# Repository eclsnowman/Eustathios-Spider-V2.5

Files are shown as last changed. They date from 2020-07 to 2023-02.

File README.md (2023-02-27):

# Eustathios-Spider-V2.5
V2.5 of Eustathios Spider (Includes Many Community Mods)

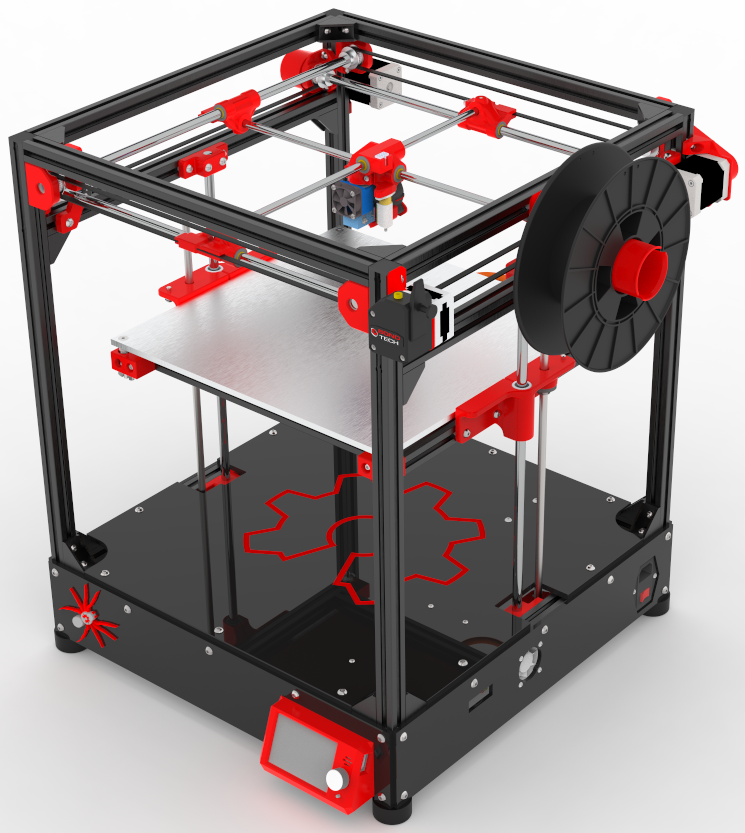
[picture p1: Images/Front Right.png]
Eustathios Spider - V2.5 Render Image


Hello and welcome to my Github for Eustathios Spider V2.5 3D printer. This printer is an updated version of the original Eustathios Spider, Eustathios Spider 2.0, and the addition of Community Modifications which have improved the design. The community added so many great improvements to this design, and I wanted to share an updated design that integrates all these wonderful improvements to the design, form, and function of this printer. I also wanted to update the design with newer more modern controls and components which have become available since the initial design.

This design stands on the shoulders of many great designers of Crossrod Gantry Printers that came before it. Most notable of these is the design of the original Eustathios by Jason Smith. This family of printers had a very devoted community in the G+ heydays, but now that Google+ has died the Community around the HercuLien printer and the Eustathios printer have moved to: https://forum.makerforums.info/c/herculien . This is thanks in great part to Michael K Johnson, who worked his magic to retain the years of great community interaction on G+ and ported it into the Discourse community over on Makerforums. If you are looking for support or community interaction on these printers moving forward, this is the place to go.

This family of printers is all based on the X/Y gantry mechanics of the Ultimaker. Ultimaker style mechanics utilizes a light hot-end/carriage which gets constrained by one X and one Y cross rod. Connected to these crossrods are rod ends which ride on side shafts that act both for power transmission of one axis (rotation) and as the linear guide for travel of the other axis (translation).

 Originally a gentleman who goes by the name Sublime (https://github.com/Intrinsically-Sublime/Tantillus/) created a small format variant of the Ultimaker mechanics which he called the Tantillus. Then GoopyPlastic (aka Brad Hill) created an extrusion version of the Tantillus called the Tslot Tantillus (https://github.com/goopyplastic/tslot-tantillus). Following in Brad’s footsteps Tim Rastall (https://plus.google.com/u/0/+TimRastall/posts) created the very popular Ingentis printer (https://www.youmagine.com/designs/ingentis-a-tantillus-variant) which is a larger version of Tantilus using thicker linear guide components, spectra drive system, and a much larger build envelope. The next printer in this design family was by Jason Smith (https://plus.google.com/u/0/103009815307828556107/posts) call the Eustathios (https://github.com/jasonsmit4/Eustathios). This is the printer that got me excited about this family of printers. Jason made several design choices like GT2 belts which I felt were great upgrades to the platform. I lucked out because his release was timed perfectly with a promotion Misumi was running where your first order from them up to $150 in value was free. I wanted to be able to modify Jason’s files slightly, but he had modeled everything in Sketchup. My limited experience was with Solidworks (self taught) so rather than learn new software I redrew Jason’s Eustathios design files from scratch. And so my Eustathios Spider V1 variant , named due to the color scheme, was born (https://github.com/eclsnowman/Lien3D_Eustathios_Spider). I built the Eustathios and fell in love with the smooth operation, clean prints, and overall reliability. So after operating the Eustathios for several months I converted my existing large CoreXY Printer (https://github.com/eclsnowman/Lien3D_CoreXY ) into a X/Y gantry printer with larger cross rods and dual extrusion. The name of this printer is HercuLien (https://github.com/eclsnowman/HercuLien). Prior to this latest revision (V2.5) there was the Eustathios Spider V2 which can be found here: https://github.com/eclsnowman/Eustathios-Spider-V2

I apologize for the long history lesson, but as you can see there is a lot of progress and talented people involved in these projects. I want to make sure credit is properly attributed to the many great makers who have come before me. The caliber of people involved and all the creativity in the platform is what keeps me so motivated. I would like to specifically mention some of the wonderful community members who added to this project over the years which have inspired or directly contributed to the Eustathios project. 

Specifically:

1.) Walter Hsiao (https://www.thingiverse.com/walter/about) for his elegant designs on the bed leveling corners, passthrough corner 6900-2RS bearing blocks, and Z Axis Bed Supports which have been integrated into the current design. In addition to these parts Walter has many additional designs for alternative components which can be used on the Eustathios like his Space Invaders Center Carriage, his Flying Extruder, and tons more. He is a prolific designer and his ability to simplify a design to its core and make it look elegant in the process inspires me and pushes me in my own designs. 

2.) Next, I would like to thank Zane Baird (https://www.linkedin.com/in/zane-baird-59096923). Over the years on Google Plus, at MRRF, and via Hangouts I am lucky to call Zane a friend. He made numerous design improvements which he implemented on his HercuLien printer. Like Water, Zane has a design style and elegance which is beyond my own ability. His designs for the Center Carriage and Side Carriages strike an balance between style and function which makes this V2.5 of the printer better than ever. Not only do these components work better and improve servicability, but they increase the printable area from previous design. Zanes input and passion on the project pushed me to do better in my own designs. I thank him for his friendship, inspiration and knowledge.

There are of course many more people to thank through this process: Martin Bondéus of Bondtech (who is a true friend with a brilliant mind), Roy Cortes from Panucatt (his boards and components are second to none), everyone from the G+ and Makerforums.info communities (Joe Spanier and Ray Kholodovsky I am looking at you), SeeMeCNC and John Olafson for years of inspiration and community through MRRF, and countless others. I can't name everyone, but you know who you are. Thank you, without you my journey of 3D Printing would not have been so fulfilling and so enjoyable.

Eustathios Spider V2.5 Overview:

* Max Travel Limits (X = 312mm / Y = 314mm / Z = 306mm)
* Designed Print Area (300mm x 300mm x 300mm)
* 32bit Controller = SKR V1.4 running Marlin 2
* TMC2209 Drivers (Qty:5) Independant Z for Marlin Auto Tram
* 24V Power with 500W Mains Powered Bed controled via SSR Relay
* Endstops:
   X&Y = switches or TMC Endstopless homing
   Z = single or dual switches, or BLTouch/3DTouch homing
* Leveling:
   Manual with endstops or autolevel w/ BLTouch/3DTouch

Documentation:

BOM = https://github.com/eclsnowman/Eustathios-Spider-V2.5/raw/master/BOM/ES25%20BOM.xlsx

Printable STL Parts = https://github.com/eclsnowman/Eustathios-Spider-V2.5/tree/master/3D%20Models/STL

Solidworks Files = https://github.com/eclsnowman/Eustathios-Spider-V2.5/tree/master/3D%20Models/Solidworks

Other 3D model formats in zip due to github file size limit) = https://github.com/eclsnowman/Eustathios-Spider-V2.5/tree/master/3D%20Models

Onshape Link: https://cad.onshape.com/documents/dcaaf87ad04323c8f9846c66/w/0537fe6b9eb1e2bc47668a76/e/4ce5ea03b6ef98527d9025d3

3D renders: https://github.com/eclsnowman/Eustathios-Spider-V2.5/tree/master/Images

Image of printed parts:

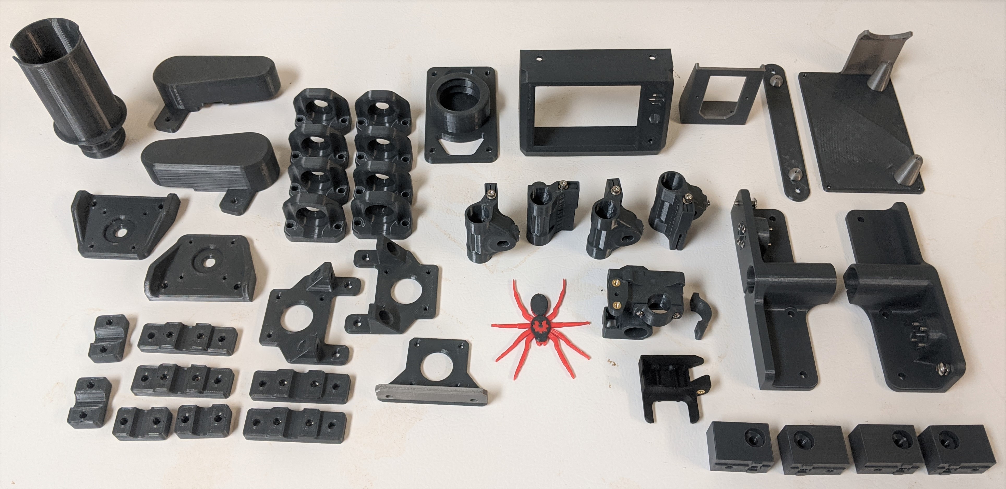
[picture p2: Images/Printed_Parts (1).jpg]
Eustathios Spider - V2.5 Printed Parts Image


Additional Renders:

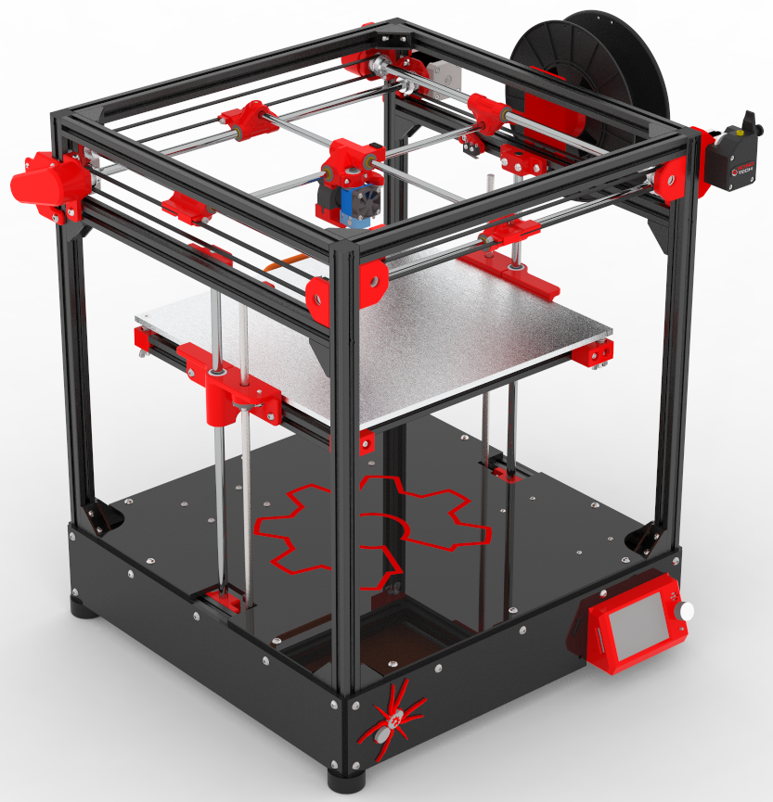
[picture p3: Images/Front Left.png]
Eustathios Spider - V2.5 Render2


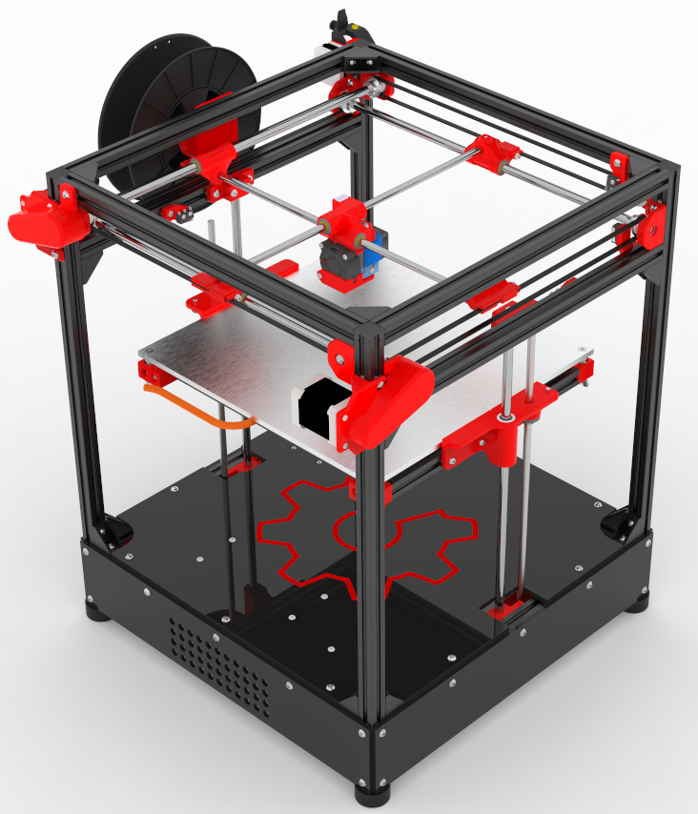
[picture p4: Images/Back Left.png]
Eustathios Spider - V2.5 Render3


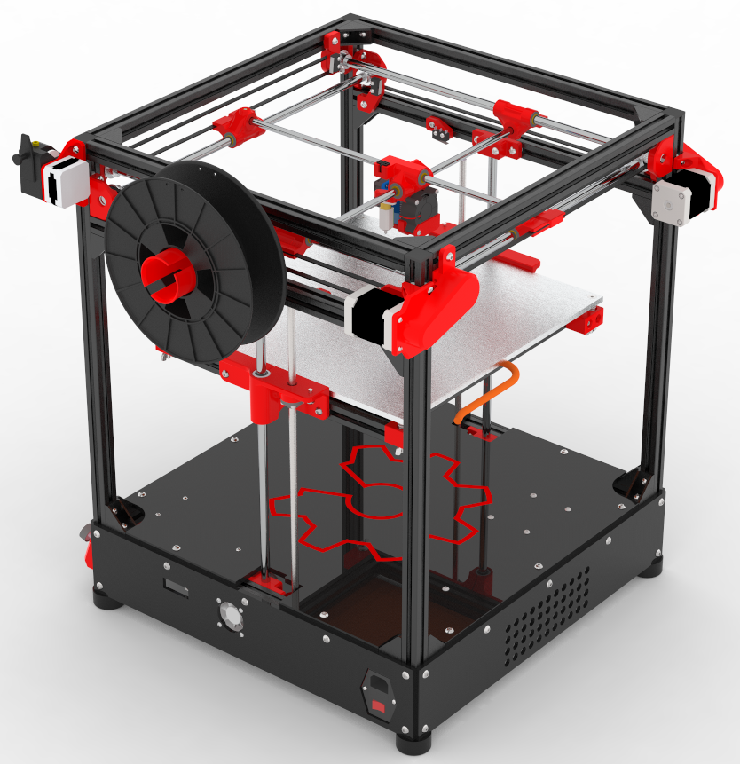
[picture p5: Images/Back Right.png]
Eustathios Spider - V2.5 Render4


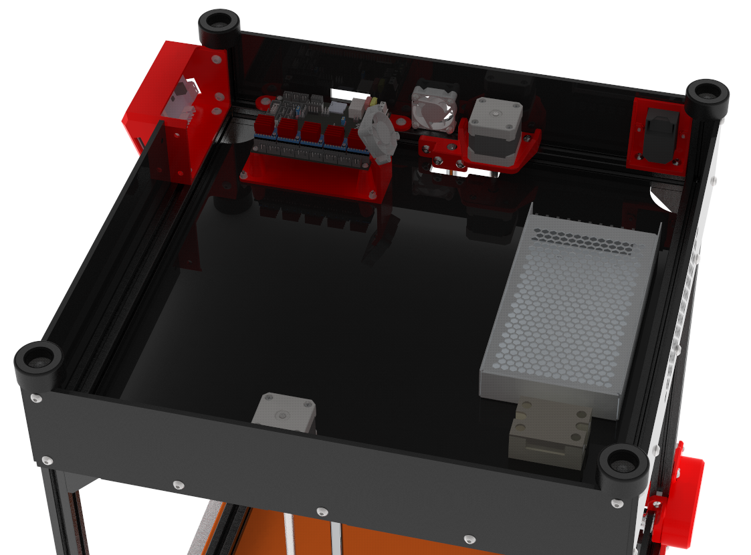
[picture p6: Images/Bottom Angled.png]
Eustathios Spider - V2.5 Render5


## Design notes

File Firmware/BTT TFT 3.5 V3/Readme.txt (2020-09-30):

Put all the contents of this folder onto a SD card formatted as fat32 and insert it into the BTT TFT35 V3. Then reboot the printer. The files and configuration will update on reboot.

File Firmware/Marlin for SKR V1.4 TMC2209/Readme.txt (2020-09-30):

This firmware.bin was built on Marlin 2.0.7 for the BTT SKR V1.4 running TMC2209 drivers and a BTT TFT35 V3. This configuration assumes you are using 1.8deg steppers on all axis, 8mm pitch lead screws on Z with independant drivers for Z1 and Z2 (Firmware has G34 enabled for auto bed tramming),a Bondtech BMG for the extruder, and a BLtouch for the probe (I am using a V2020 triangle labs3D Touch, not a BLTouch). All microstepping has been set for 32 in the firmware, and current have been configured based on reliable operation on my printer. If you modify the marlin firmware and make changes you do so at your own risk. That being said. If you find configuration improvements please submit a pull request for me to review to integrate into the project.

Have Fun,

ECL 09-30-20

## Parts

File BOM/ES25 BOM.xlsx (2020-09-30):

QTY. | PART | DESCRIPTION | Vendor | Price/EA | Price (Lot) | Link | Alternate Source = Link 2
8 | Bearing Holder with Pass Through | 3D Printed 6900-2RS Bearing Holder | 3D Printed | $0.00 | $0.00 | https://github.com/eclsnowman/Eustathios-Spider-V2.5/tree/master/3D%20Models/STL
2 | Bed Mount Block | 3D Printed Bed Mounting Corner Block | 3D Printed | $0.00 | $0.00 | https://github.com/eclsnowman/Eustathios-Spider-V2.5/tree/master/3D%20Models/STL
2 | Bed Mount Block (Mirrored) | 3D Printed Bed Mounting Corner Block | 3D Printed | $0.00 | $0.00 | https://github.com/eclsnowman/Eustathios-Spider-V2.5/tree/master/3D%20Models/STL
1 | Belt Guard A | 3D Printed Belt Guard A | 3D Printed | $0.00 | $0.00 | https://github.com/eclsnowman/Eustathios-Spider-V2.5/tree/master/3D%20Models/STL
1 | Belt Guard B | 3D Printed Belt Guard B | 3D Printed | $0.00 | $0.00 | https://github.com/eclsnowman/Eustathios-Spider-V2.5/tree/master/3D%20Models/STL
1 | BMG Mount | 3D Printed Bondtech BMG Mount | 3D Printed | $0.00 | $0.00 | https://github.com/eclsnowman/Eustathios-Spider-V2.5/tree/master/3D%20Models/STL
1 | Center Carriage With BLTouch | 3D Gantry Center Carriage | 3D Printed | $0.00 | $0.00 | https://github.com/eclsnowman/Eustathios-Spider-V2.5/tree/master/3D%20Models/STL
1 | Cooling Duct v2 | 3D Printed Cooling Duct V2 | 3D Printed | $0.00 | $0.00 | https://github.com/eclsnowman/Eustathios-Spider-V2.5/tree/master/3D%20Models/STL
1 | LCD Cover BBT TFT35 V3 | 3D printed LCD Cover for BBT TFT35 V3 | 3D Printed | $0.00 | $0.00 | https://github.com/eclsnowman/Eustathios-Spider-V2.5/tree/master/3D%20Models/STL
1 | Outlet Switch Mount | 3D printed IEC Fused Switched Mount | 3D Printed | $0.00 | $0.00 | https://github.com/eclsnowman/Eustathios-Spider-V2.5/tree/master/3D%20Models/STL
1 | SKR 1.3 / 1.4 Controller Mount | 3D printed SKR Controller Mount | 3D Printed | $0.00 | $0.00 | https://github.com/eclsnowman/Eustathios-Spider-V2.5/tree/master/3D%20Models/STL
1 | Spider Logo 2 | 3D Printed Spider Logo (Visual Only, Not Required) | 3D Printed | $0.00 | $0.00 | https://github.com/eclsnowman/Eustathios-Spider-V2.5/tree/master/3D%20Models/STL
1 | Spool Holder Threaded Flange | 3D printed Threaded Spool Holder Flange for Eustathios | 3D Printed | $0.00 | $0.00 | https://github.com/eclsnowman/Eustathios-Spider-V2.5/tree/master/3D%20Models/STL
1 | Threaded Spool Holder Insert | 3D Printed Insert for Spool Holder, Various Lengths and Diameters Availible | 3D Printed | $0.00 | $0.00 | https://github.com/eclsnowman/Eustathios-Spider-V2.5/tree/master/3D%20Models/STL
1 | X (NEW) Endstop Mount | 3D Printed X Axis Endstop Mount (Not needed if Endstopless Homeing is Enabled on TMC 2209) | 3D Printed | $0.00 | $0.00 | https://github.com/eclsnowman/Eustathios-Spider-V2.5/tree/master/3D%20Models/STL
2 | XY External Motor Mount | 3D printed X / Y Motor Mount | 3D Printed | $0.00 | $0.00 | https://github.com/eclsnowman/Eustathios-Spider-V2.5/tree/master/3D%20Models/STL
2 | XY Side Carriage Zane V2.5 Rev2 | 3D Printed X and Y Axis Gantry Side Carriages | 3D Printed | $0.00 | $0.00 | https://github.com/eclsnowman/Eustathios-Spider-V2.5/tree/master/3D%20Models/STL
2 | XY Side Carriage Zane V2.5 Rev2 (Mirrored) | 3D Printed X and Y Axis Gantry Side Carriages | 3D Printed | $0.00 | $0.00 | https://github.com/eclsnowman/Eustathios-Spider-V2.5/tree/master/3D%20Models/STL
1 | Y (New) Endstop Mount | 3D Printed Y Axis Endstop Mount (Not needed if Endstopless Homeing is Enabled on TMC 2209) | 3D Printed | $0.00 | $0.00 | https://github.com/eclsnowman/Eustathios-Spider-V2.5/tree/master/3D%20Models/STL
2 | Z (NEW) Endstop Mount | 3D Printed Z Axis Endstop Mount (Not needed if BLTouch is wired as Z Probe) | 3D Printed | $0.00 | $0.00 | https://github.com/eclsnowman/Eustathios-Spider-V2.5/tree/master/3D%20Models/STL
2 | Z Axis Bed Support V2.5 | 3D Printed Z Axis Bed Support | 3D Printed | $0.00 | $0.00 | https://github.com/eclsnowman/Eustathios-Spider-V2.5/tree/master/3D%20Models/STL
4 | Z Axis Shaft Mount A | 3D Printed Z Axis Shaft Mount A | 3D Printed | $0.00 | $0.00 | https://github.com/eclsnowman/Eustathios-Spider-V2.5/tree/master/3D%20Models/STL
4 | Z Axis Shaft Mount B | 3D Printed Z Axis Shaft Mount A | 3D Printed | $0.00 | $0.00 | https://github.com/eclsnowman/Eustathios-Spider-V2.5/tree/master/3D%20Models/STL
2 | Z Integrated Leadscrew Motor Mount | 3D Printed Z Axis Integrated Lead Screw Motor Mount | 3D Printed | $0.00 | $0.00 | https://github.com/eclsnowman/Eustathios-Spider-V2.5/tree/master/3D%20Models/STL
1 | 320x320 120VAC 500W Heated Bed | Purchase From Alirubber On Alibaba, $22.50 USD + $25 Shiping To USA | Alirubber | $19.58 | $19.58 | https://www.alibaba.com/product-detail/320-320mm-120V-500W-Custom-Silicone_1600085794450.html | https://keenovo.store/
1 | 4020 Blower Fan 24V | 4020 Blower Fan, 24V | Amazon | $5.00 | $19.98 | https://www.amazon.com/WINSINN-40x20mm-Brushless-Cooling-Extruder/dp/B07L2YH79Y
2 | 40x40x10 Axial 24V Fan | 4010 Axial Fan, 24V | Amazon | $4.00 | $19.98 | https://www.amazon.com/WINSINN-40x40x10mm-Brushless-Extruder-Makerbot/dp/B07DB5H6K1
1 | IEC Fused Switched Plug | IEC 10A 250V Fused Receptical with Switch | Amazon | $6.99 | $6.99 | https://www.amazon.com/URBEST-Rocker-Switch-IEC320-Module/dp/B00NWO68JI
4 | Micro Switch Button | Microwitch (Drill mounting holes out to 3mm) | Amazon | $0.45 | $8.96 | https://www.amazon.com/Switch-Action-250VAC-Terminals-Momentary/dp/B0778GPX39
2 | TR8x8 POM Lead Nut | TR8x8 POM Nut | Amazon | $8.99 |  | https://www.amazon.com/Befenybay-Trapezoidal-Delrin-Printer-Accessory/dp/B07RJT1GD8
2 | 380mm_TR8x8_42mm_Nema17 | 380mm TR8x8 Integrated Leadscrew Stepper | Banggood | $26.78 | $53.56 | https://usa.banggood.com/Machifit-Nema17-42mm-Stepper-Motor-with-T8-380mm-Lead-Screw-for-CNC-Engraving-Machine-p-1409514.html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
1 | BTT_SKR_V1.4 | SKR V1.4 Turbo w/ TMC2209 and TFT35 V3.0 (Buy Individually or in kit with Display) | BigTreeTech | $73.45 | $73.45 | https://www.biqu.equipment/products/btt-skr-v1-4-skr-v1-4-pro?variant=31220354416738 | https://www.amazon.com/BIGTREETECH-Direct-5pcsTMC2209-LPC1769-120MHz-Frequency/dp/B082X998S2
1 | TFT 3.5 V3 +WIFI | BigTreeTech TFT35 V3.0 (Recommended to get it in a bundle for cheaper pricing. | BigTreeTech | $0.00 | $0.00 | See SKR 1.3 / 1.4 Bundle Above
5 | TMC2209 | TMC 2209 Drivers (Recommended to get it in a bundle for cheaper pricing) | BigTreeTech | $0.00 | $0.00 | See SKR 1.3 / 1.4 Bundle Above
1 | Bondtech_BMG | Bondtech BMG (Needs Motor) | Bondtech | $80.00 | $80.00 | https://www.bondtech.se/en/product/bmg-extruder/
1 | 0430200801 | 8 position Male Molex Microfit 3.0 Connector | Digikey | $0.51 | $0.51 | https://www.digikey.com/product-detail/en/molex/0430200801/WM2763-ND/1132439
1 | 0430250808 | 8 position Female Molex Microfit 3.0 Connector | Digikey | $0.67 | $0.67 | https://www.digikey.com/product-detail/en/molex/0430250808/WM13210-ND/3310166
10 | 0430300002 | Female Molex Microfit 3.0 Crimp Pins | Digikey | $0.16 | $1.58 | https://www.digikey.com/product-detail/en/molex/0430300002/WM1125CT-ND/467811
10 | 0430310002 | Male Molex Microfit 3.0 Crimp Pins | Digikey | $0.18 | $1.84 | https://www.digikey.com/product-detail/en/molex/0430310002/WM1127CT-ND/467813
1 | Panel_Back_Bottom | Black Acrylic 1/4" (or 6mm) Panels | Fabricated (laser cut or 1:1 template cutour by hand) | $7.29 | $7.29 | https://www.amazon.com/24-Black-Acrylic-Plexiglass-Opaque/dp/B00IWACJ3Q
1 | Panel_Bottom_Plate | Black Acrylic 1/4" (or 6mm) Panels | Fabricated (laser cut or 1:1 template cutour by hand) | $29.15 | $29.15 | https://www.amazon.com/24-Black-Acrylic-Plexiglass-Opaque/dp/B00IWACJ3Q
1 | Panel_Front_Bottom | Black Acrylic 1/4" (or 6mm) Panels | Fabricated (laser cut or 1:1 template cutour by hand) | $7.29 | $7.29 | https://www.amazon.com/24-Black-Acrylic-Plexiglass-Opaque/dp/B00IWACJ3Q
1 | Panel_Left_Bottom | Black Acrylic 1/4" (or 6mm) Panels | Fabricated (laser cut or 1:1 template cutour by hand) | $7.29 | $7.29 | https://www.amazon.com/24-Black-Acrylic-Plexiglass-Opaque/dp/B00IWACJ3Q
1 | Panel_Right_Bottom | Black Acrylic 1/4" (or 6mm) Panels | Fabricated (laser cut or 1:1 template cutour by hand) | $7.29 | $7.29 | https://www.amazon.com/24-Black-Acrylic-Plexiglass-Opaque/dp/B00IWACJ3Q
8 | 6900-2RS | 10x22x6 2RS Bearing (10pk) | Fast Eddy Bearings | $1.00 | $9.99 | https://www.fasteddybearings.com/10-units-10x22x6-rubber-sealed-bearing-6900-2rs/
1 | Aluminum Heat Spreader Build Plate (358mm x 346mm) | 358mm x 346mm - Custom Fabricated 0.25in Cast Aluminum Build Plate | Howard Precision Metals or Midwest Steel and Aluminum | $42.72 | $42.72 | https://www.midweststeelsupply.com/store/castaluminumplateatp5 | https://www.howardprecision.com/aluminum/aluminum-cast-tool-jig-plate-stock-list/mic-6-aluminum/
4 | 2032N24 | 8mm ID x 15.9mm OD Bronze Misalignment Bushing. | McMaster Carr | $4.76 | $19.04 | https://www.mcmaster.com/2032N24/
8 | 2032N25 | 10mm ID x 15.9mm OD Bronze Misalignment Bushing. | McMaster Carr | $4.41 | $35.28 | https://www.mcmaster.com/2032N25/
4 | 9002T427 | Compression Spring (3pk)(1" Long, 0.3" OD, 0.216" ID, 302 Stainless Steel) | McMaster Carr | $1.99 | $11.92 | https://www.mcmaster.com/9002T427/
8 | 90214A422 | Stainless 10mm ID x 16mm OD x 0.5mm Shim (Comes in 10pack) | McMaster Carr | $1.23 | $12.31 | https://www.mcmaster.com/90214A422/
4 | 92125A226 | 5mm x 45mm SST Hex Drive Flat Head | McMaster Carr | $0.36 | $9.12 | https://www.mcmaster.com/92125A226/
4 | 92605A102 | 3mm x 8mm SST Flat Tip Set Screw | McMaster Carr | $0.13 | $3.13 | https://www.mcmaster.com/92605A102/
13 | 94180A333 | 3mm x 6.4mm D Heat Set Insert (100pk) | McMaster Carr | $0.17 | $16.69 | https://www.mcmaster.com/94180A333/
4 | 9540k28 | Rubber Feet 1.5" OD x 0.75in H | McMaster Carr | $0.97 | $9.73 | https://www.mcmaster.com/9540K28/
16 | HBLFSNB5 | 20x20 Corner Bracket | Misumi | $1.98 | $31.68 | https://us.misumi-ec.com/vona2/detail/110300437260/?ProductCode=HBLFSNB5 | https://www.robotdigg.com/product/371/Connect-Fittings-for-2020-or-3030-alu-profile
4 | HFC5-2020-B | 20x20 Extrusion End Caps (Can 3d Print Instead, see Thingiverse for examples) | Misumi | $1.97 | $7.88 | https://us.misumi-ec.com/vona2/detail/110300440510/?ProductCode=HFC5-2020-B | https://www.thingiverse.com/thing:813368
2 | HFSB5-2020-296.5-TPW | 20x20 Black Extrusion 296.5mm (Both Ends Tapped) | Misumi | $6.68 | $13.36 | https://us.misumi-ec.com/vona2/detail/110302683830/?ProductCode=HFSB5-2020-296.5-TPW
2 | HFSB5-2020-321 | 20x20 Black Extrusion 321mm | Misumi | $3.27 | $6.54 | https://us.misumi-ec.com/vona2/detail/110302683830/?ProductCode=HFSB5-2020-321
10 | HFSB5-2020-425-TPW | 20x20x425 Black Extrusion (Both Ends Tapped) | Misumi | $7.93 | $79.30 | https://us.misumi-ec.com/vona2/detail/110302683830/?ProductCode=HFSB5-2020-425-TPW
4 | HFSB5-2020-562-LTP-RCP-FR-AH470-AP80 | 20x20x562 Black Extrusion With Cross Holes | Misumi | $14.47 | $57.89 | https://us.misumi-ec.com/vona2/detail/110302683830/?ProductCode=HFSB5-2020-562-LTP-RCP-FR-AH470-AP80
2 | SFJ10-435 | 10mm x 435mm Precision Linear Shaft (G6 Fit) | Misumi | $13.73 | $27.46 | https://us.misumi-ec.com/vona2/detail/110302634310/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
2 | SFJ10-458 | 10mm x 458mm Precision Linear Shaft (G6 Fit) | Misumi | $13.73 | $27.46 | https://us.misumi-ec.com/vona2/detail/110302634310/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
2 | SFJ10-483 | 10mm x 483mm Precision Linear Shaft (G6 Fit) | Misumi | $13.73 | $27.46 | https://us.misumi-ec.com/vona2/detail/110302634310/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
2 | SFJ8-410 | 8mm x 410mm Precision Linear Shaft (G6 Fit) | Misumi | $13.41 | $26.82 | https://us.misumi-ec.com/vona2/detail/110302634310/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
1 | Meanwell LRS-200-24 | Meanwell 24V 200W PSU (LRS-200-24) | Mouser Electronics | $25.71 | $25.71 | https://www.mouser.com/ProductDetail/MEAN-WELL/LRS-200-24?qs=ah3jBNVE1PQukNhKX3jUsA%3D%3D | https://www.amazon.com/MEAN-WELL-LRS-200-24-211-2W-Switchable/dp/B00YMA7I7C?s=industrial
1 | G3NA_220B | Omron G3NA_220B SSR | Newark | $30.52 | $30.52 | https://www.newark.com/omron-industrial-automation/g3na-220b-dc5-24/ssr-panel-mount-264vac-24vdc-20a/dp/17M6661 | https://www.amazon.com/Omron-G3NA-220B-AC100-120-Indicator-Photocoupler-Isolation/dp/B005T786P0?s=industrial
2 | GT2_Aluminum_Timing_Pulley_20_Tooth | 20 Tooth GT2 Pulley (5mm Bore) | Printed Solid or Robotdigg | $5.00 | $10.00 | https://www.printedsolid.com/products/ldo-2gt-pulley-with-5mm-bore | https://www.robotdigg.com/product/226/20-Tooth-2GT-Pulley-10pcs-per-lot
1 | BLTouch or 3DTouch | BLTouch Bed Leveling Touch Probe | Printed Solid or Trianglelab | $34.98 | $34.98 | https://www.aliexpress.com/item/32832887426.html | https://www.printedsolid.com/products/bltouch-automatic-bed-leveling-probe
1 | Bowden Tube | Bowden Tube for 1.75mm Filament (1M) | Printed Solid or Trianglelab | $10.99 | $10.99 | https://www.printedsolid.com/products/capricorn-xs-reduced-friction-bowden-tubing?variant=47610453836 | https://www.aliexpress.com/item/32811240720.html?spm=2114.12010610.8148356.3.510d6ff09MSsfJ
1 | E3D V6 24V with Sock | E3D V6 24 | Printed Solid or Trianglelab | $61.90 | $61.90 | https://www.printedsolid.com/products/e3d-hot-end-kit-v6?variant=22124029083733 | https://www.aliexpress.com/item/32844028127.html?spm=2114.12010610.8148356.6.510d6ff02qrX5f
10 | 10mm_ID x 32T GT2 Pulley | 10mm_ID x 32T GT2 Pulley | Robotdigg | $1.60 | $16.00 | https://www.robotdigg.com/product/149/10mm-bore-32-teeth-gt2-pulley | https://us.misumi-ec.com/vona2/detail/110302193470/?ProductCode=GPA32GT2060-A-P10
138 | 2020 M5 Solid Tslot Nut | 20x20 M5 Pre-Assebly Tslot Nuts (100pk) | Robotdigg | $0.07 | $15.00 | https://www.robotdigg.com/product/317/Pre-assembly-T-nuts-for-2020-or-3030-alu-profile | https://www.amazon.com/KOOTANS-Assembly-Fastener-Aluminum-Extrusion/dp/B07PQ13LCQ
4 | 850mm GT2 6mm Wide Belt Open Loop | GT2 6mm Wide Belt Open Loop (5m Pk) | Robotdigg | $1.02 | $6.00 | https://www.robotdigg.com/product/10/Open-Ended-6mm-Width-GT2-Belt | https://us.misumi-ec.com/vona2/detail/110302652060/?ProductCode=GBN9002GT-60
2 | GT2 XY Drive Belts (180mm 90tooth) | GT2 180mm (90 tooth) GT2 x 6mm Closed Loop Belt | Robotdigg | $0.35 | $0.70 | https://www.robotdigg.com/product/280/180mm-or-186mm-2GT-endless-belt | https://us.misumi-ec.com/vona2/detail/110302652060/?ProductCode=GBN1802GT-60
2 | LM10LUU | Linear Bearing (Long) (10mm ID x 19mm OD x 55mm Long) | Robotdigg | $1.50 | $3.00 | https://www.robotdigg.com/product/362/LM10LUU-Linear-Bearing | https://us.misumi-ec.com/vona2/detail/110300026540/?ProductCode=LMUW10
1 | Extruder Motor | Nema17 Extruder Stepper Motor for BMG | Robotdigg or Printed Solid | $6.60 | $6.60 | https://www.robotdigg.com/product/7/NEMA17-40mm-long-17hs3001-20b-Stepper-Motor | https://www.printedsolid.com/collections/motors/products/ldo-nema-17-motor-high-temp-180c-ldo-42sth40-1004ah
2 | X and Y Motors | Nema17 60mm Drive Motors | Robotdigg or Printed Solid | $10.90 | $21.80 | https://www.robotdigg.com/product/29/Nema17-60mm-1.5A-high-torque-stepper-motor | https://www.printedsolid.com/products/ldo-nema-17-motor-supermac-ldo-42sth60-2004ac
2 | 3mm x 04mm SST SCS | 3mm x 04mm SST SCS (25pk) | Trimcraft Aviation RC | $0.02 | $0.62 | http://www.trimcraftaviationrc.com/index.php?route=product/product&path=24_18_37&product_id=433
4 | 3mm x 06mm SST BSC | 3mm x 6mm SST BSC (25pk) | Trimcraft Aviation RC | $0.02 | $0.49 | http://www.trimcraftaviationrc.com/index.php?route=product/product&path=24_2_27&product_id=24
10 | 3mm x 08mm SST BSC | 3mm x 8mm SST BSC (25pk) | Trimcraft Aviation RC | $0.03 | $0.64 | http://www.trimcraftaviationrc.com/index.php?route=product/product&path=24_2_27&product_id=25
16 | 3mm x 10mm SST BSC | 3mm x 10mm SST BSC (25pk) | Trimcraft Aviation RC | $0.03 | $0.67 | http://www.trimcraftaviationrc.com/index.php?route=product/product&path=24_2_27&product_id=37
8 | 3mm x 12mm SST BSC | 3mm x 12mm SST BSC (25pk) | Trimcraft Aviation RC | $0.03 | $0.83 | http://www.trimcraftaviationrc.com/index.php?route=product/product&path=24_2_27&product_id=23
2 | 3mm x 14mm SST BSC | 3mm x 14mm SST BSC (25pk) | Trimcraft Aviation RC | $0.03 | $0.65 | http://www.trimcraftaviationrc.com/index.php?route=product/product&path=24_2_27&product_id=508
8 | 3mm x 14mm SST SCS | 3mm x 14mm SST SCS (25pk) | Trimcraft Aviation RC | $0.02 | $0.62 | http://www.trimcraftaviationrc.com/index.php?route=product/product&path=24_18_37&product_id=190
8 | 3mm x 16mm SST BSC | 3mm x 16mm SST BSC (25pk) | Trimcraft Aviation RC | $0.03 | $0.87 | http://www.trimcraftaviationrc.com/index.php?route=product/product&path=24_2_27&product_id=26
6 | 3mm x 20mm SST BSC | 3mm x 20mm SST BSC (25pk) | Trimcraft Aviation RC | $0.04 | $1.00 | http://www.trimcraftaviationrc.com/index.php?route=product/product&path=24_2_27&product_id=27
1 | 3mm x 25mm SST BSC | 3mm x 25mm SST BSC (25pk) | Trimcraft Aviation RC | $0.04 | $1.04 | http://www.trimcraftaviationrc.com/index.php?route=product/product&path=24_2_27&product_id=502
2 | 3mm x 35mm SST SCS | 3mm x 35mm SST SCS (12pk) | Trimcraft Aviation RC | $0.06 | $0.72 | http://www.trimcraftaviationrc.com/index.php?route=product/product&path=24_18_37&product_id=194
4 | 4mm x 08mm SST BSC | 4mm x 08mm SST BSC (25pk) | Trimcraft Aviation RC | $0.02 | $0.58 | http://www.trimcraftaviationrc.com/index.php?route=product/product&path=24_2_27&product_id=28
2 | 4mm x 16mm SST BSC | 4mm x 16mm SST BSC (25pk) | Trimcraft Aviation RC | $0.04 | $0.93 | http://www.trimcraftaviationrc.com/index.php?route=product/product&path=24_2_27&product_id=30
6 | 5mm x 08mm SST BSC | 5mm x 8mm SST BSC (12pk) | Trimcraft Aviation RC | $0.05 | $0.56 | http://www.trimcraftaviationrc.com/index.php?route=product/product&path=24_2_27&product_id=487
121 | 5mm x 10mm SST BSC | 5mm x 10mm SST BSC (12pk) | Trimcraft Aviation RC | $0.05 | $6.16 | http://www.trimcraftaviationrc.com/index.php?route=product/product&path=24_2_27&product_id=456
26 | 5mm x 12mm SST BSC | 5mm x 12mm SST BSC (12pk) | Trimcraft Aviation RC | $0.06 | $1.98 | http://www.trimcraftaviationrc.com/index.php?route=product/product&path=24_2_27&product_id=457
7 | 5mm x 14mm SST BSC | 5mm x 14mm SST BSC (12pk) | Trimcraft Aviation RC | $0.06 | $0.67 | http://www.trimcraftaviationrc.com/index.php?route=product/product&path=24_2_27&product_id=50
4 | 5mm x 16mm SST BSC | 5mm x 16mm SST BSC (12pk) | Trimcraft Aviation RC | $0.06 | $0.67 | http://www.trimcraftaviationrc.com/index.php?route=product/product&path=24_2_27&product_id=52
8 | 5mm x 20mm SST BSC | 5mm x 20mm SST BSC (12pk) | Trimcraft Aviation RC | $0.06 | $0.69 | http://www.trimcraftaviationrc.com/index.php?route=product/product&path=24_2_27&product_id=484
4 | 5mm x 25mm SST BSC | 5mm x 25mm SST BSC (12pk) | Trimcraft Aviation RC | $0.07 | $0.84 | http://www.trimcraftaviationrc.com/index.php?route=product/product&path=24_2_27&product_id=467
4 | 94545A225 | 5mm SST Wing Nut | Trimcraft Aviation RC | $0.11 | $0.44 | http://www.trimcraftaviationrc.com/index.php?route=product/product&path=72&product_id=455 | https://www.mcmaster.com/94545A225/
8 | M3 Flat Washer | M3 Flat Washer SST (25pk) | Trimcraft Aviation RC | $0.01 | $0.15 | http://www.trimcraftaviationrc.com/index.php?route=product/product&path=6_52_57&product_id=230
8 | M3 Nylock Nut | M3 Nylock Nut SST (25pk) | Trimcraft Aviation RC | $0.02 | $0.41 | http://www.trimcraftaviationrc.com/index.php?route=product/product&path=7_29&product_id=234
2 | M4 Nylock Nut | M4 Nylock Nut SST (25pk) | Trimcraft Aviation RC | $0.03 | $0.66 | http://www.trimcraftaviationrc.com/index.php?route=product/product&path=7_29&product_id=235
4 | M5 Flat Fender Washer | M5 Flat Fender Washer SST (25pk) | Trimcraft Aviation RC | $0.03 | $0.64 | http://www.trimcraftaviationrc.com/index.php?route=product/product&path=6_52_57&product_id=459
8 | M5 Flat Washer | M5 Flat Washer SST (25pk) | Trimcraft Aviation RC | $0.01 | $0.20 | http://www.trimcraftaviationrc.com/index.php?route=product/product&path=6_52_57&product_id=231
2 | M5 Jam Nut | M5 Jam Nut SST (25pk) | Trimcraft Aviation RC | $0.02 | $0.56 | http://www.trimcraftaviationrc.com/index.php?route=product/product&product_id=466&search=jam
12 | M5 Nylock Nut | M5 Nylock Nut SST (25pk) | Trimcraft Aviation RC | $0.03 | $0.69 | http://www.trimcraftaviationrc.com/index.php?route=product/product&path=7_29&product_id=236
 |  |  |  | Total | $1089.36
 | Options
1 | 350 x 350mm Sprint Steel PEI Bed and Magnet (One Side Smooth, One Side Textured) | 350 x 350 Spring Steel PEI Bed | ENERGTIC 3D Store | $60.12 | $60.12 | https://www.aliexpress.com/item/4000182312858.html?spm=2114.12010612.8148356.55.720837a579aYPw
1 | Change from a Bondtech BMG to Bondtech QR Extruder (if you change to QR you no longer need the motor for the BMG) | Bondtech QR Extruder | Bondtech | $155.00 | $155.00 | https://www.bondtech.se/en/product/qr/
 | Misc Vitamines and Other Parts
 | Misc Wiring (not specified) | Please confirm you wire with proper gauge, wire type, impliment proper grounding, and use stain relief. Tutorials on wiring are beyond the scope of this printer design. Please be careful and if you do not know what to do (especially with mains wiring) ask for assistance from a knowledgable friend. |  |  |  | https://www.amazon.com/stores/BNTECHGO/page/62B1C820-10D9-448B-916B-BD7817990918?ref_=ast_bln
 | Change Log:
R1 | Updated 07-14-20, User noted I was missing X/Y Motors. I added them to the sheet

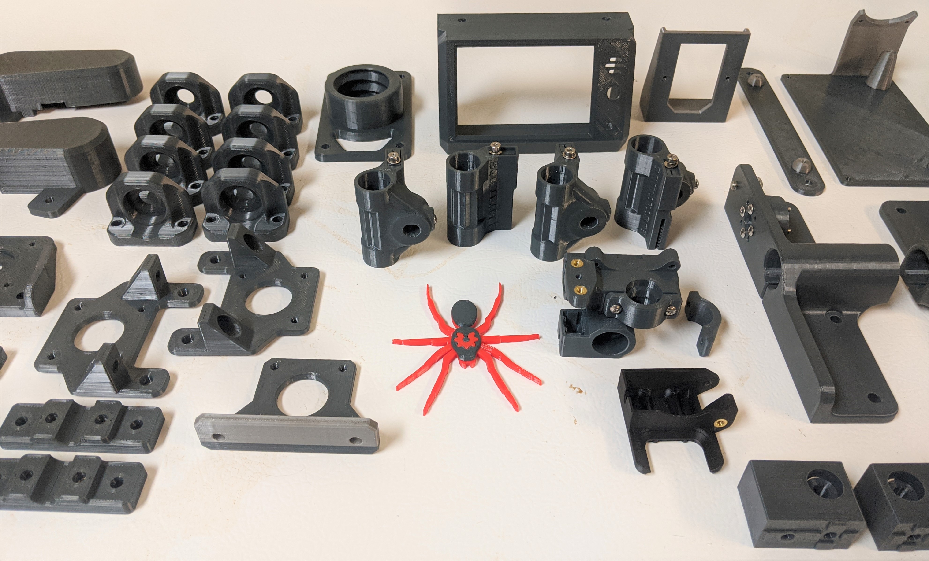
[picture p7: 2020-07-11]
Images/Printed_Parts (3).jpg

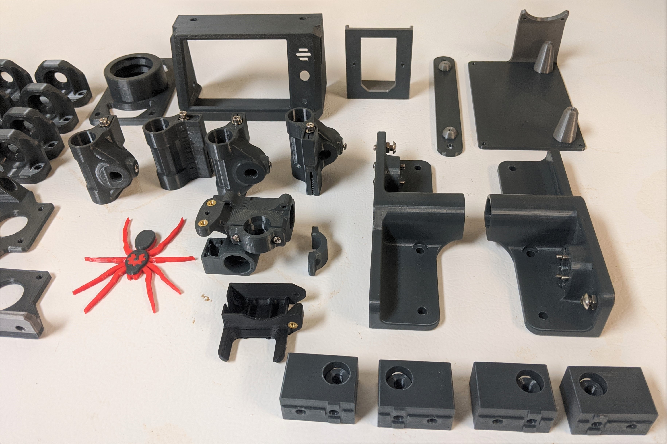
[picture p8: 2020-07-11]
Images/Printed_Parts (4).jpg

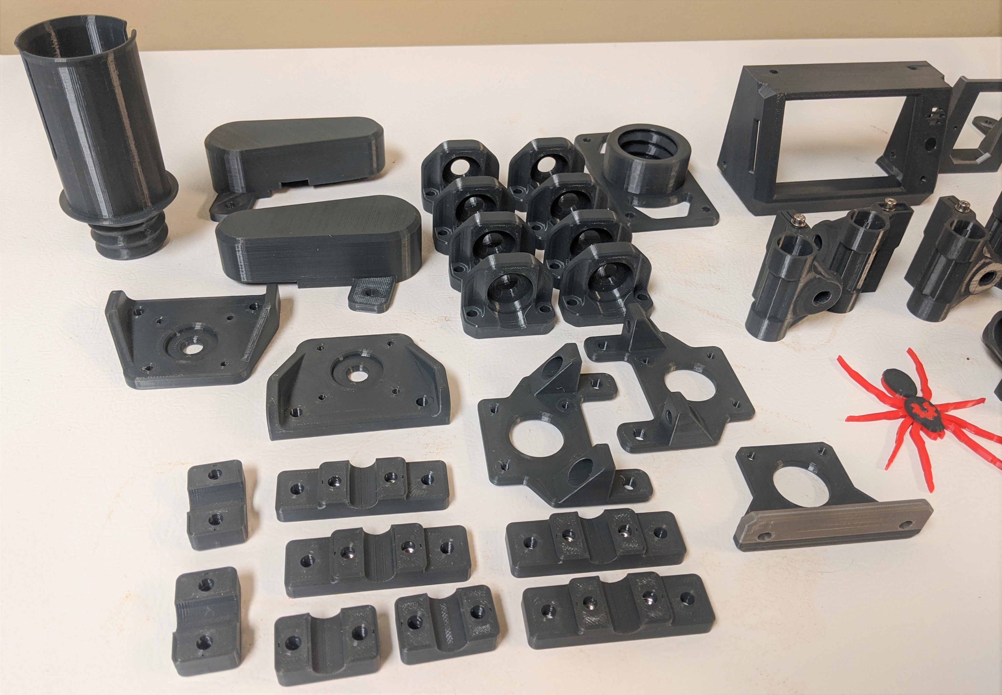
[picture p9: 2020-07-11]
Images/Printed_Parts (2).jpg

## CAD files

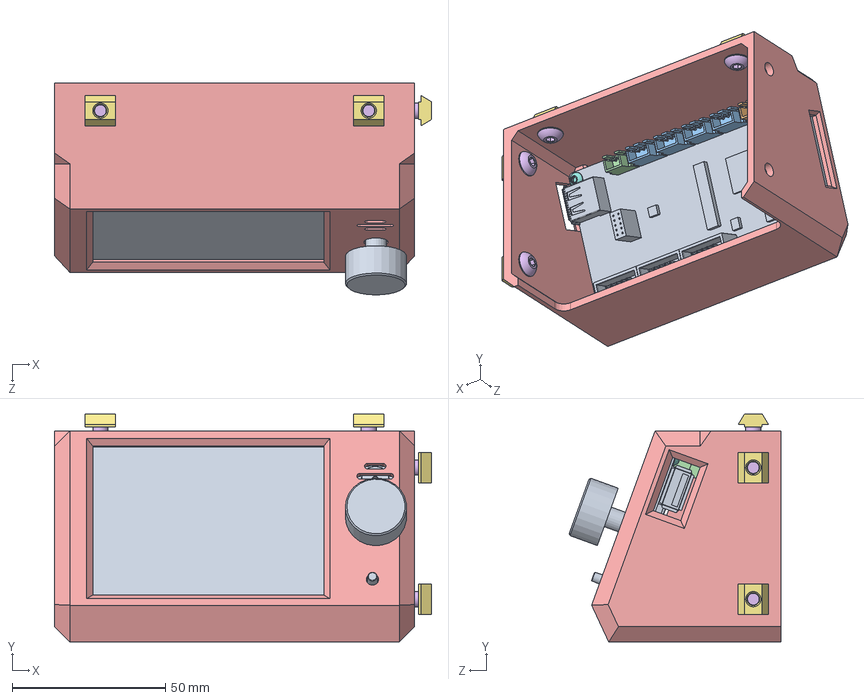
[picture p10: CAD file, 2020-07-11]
3D Models/Solidworks/Electronics/BTT/BTT TFT35 V3 Cover/LCD and Cover.SLDASM
123.2 x 74.5 x 69.2 mm
TFT 3.5 V3 +WIFI
KONEKTOR TFT35 PIN5 x 2
KONEKTOR TFT35 PIN3 x 4
KONEKTOR TFT35 PIN2
LCD Cover BBT TFT35 V3
Trimcraft M5 BSC x 4
M5 Tslot Nut x 4
Trimcraft M3 BSC x 4

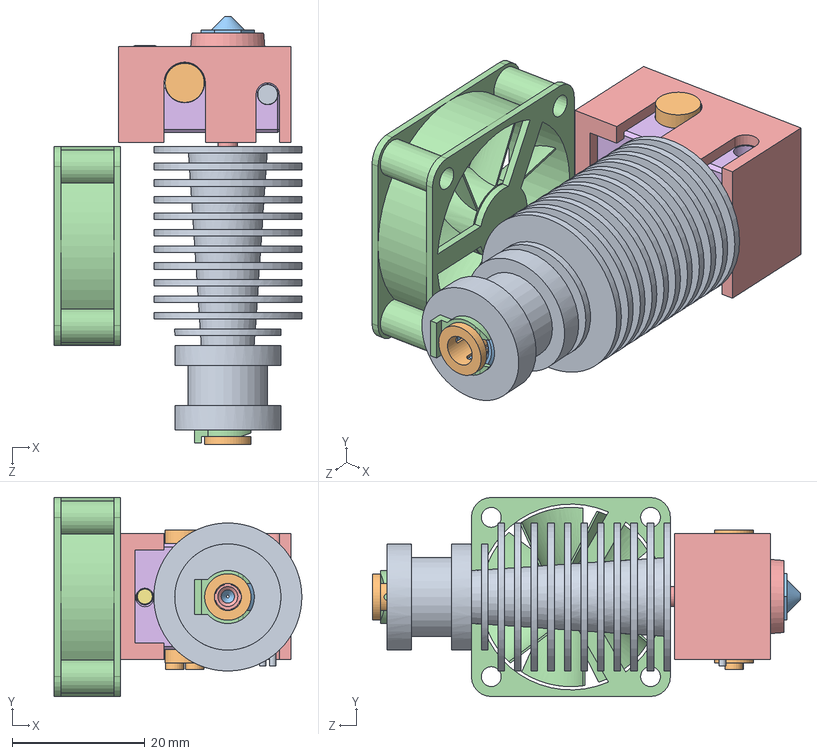
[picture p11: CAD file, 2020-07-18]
3D Models/Solidworks/Electronics/E3D/V6 Model/e3D V6 1.75mm Hotend Assembly.SLDASM
37.3 x 30.0 x 64.5 mm
V6-175-SINK
Collet
Coupling
Collet Clip
V6-Heatbreak
V6-Heatblock
M3x10 rounded head screw - 92095A182 (1)
M3x4 flat tip set screw - 92605A098
Thermistor
Heater Cartridge
V6-175-Nozzle 0.4mm
30x10mm box fan
E3D Sock

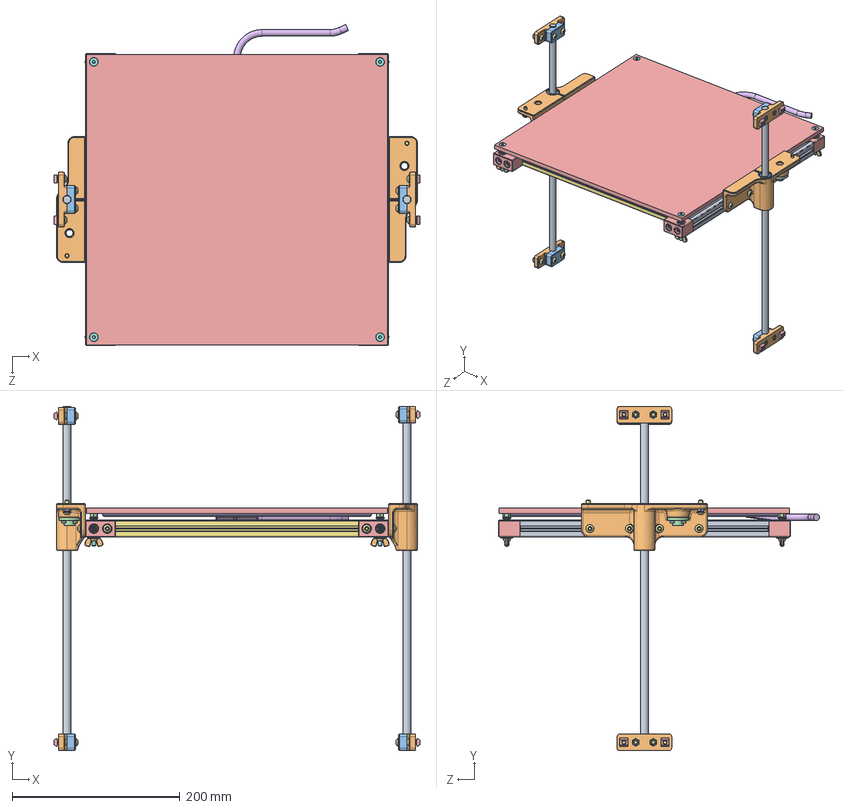
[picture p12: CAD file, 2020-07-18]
3D Models/Solidworks/Sub Assemblies/Z_Axis_And_Bed.SLDASM
436.0 x 410.3 x 382.5 mm
HFSB5-2020-296.5-TPW x 2
Z_Axis_Bed_Support V2.5 x 2
LM10LUU x 2
TR8x8 POM Lead Nut x 2
M5 Tslot Nut x 20
Trimcraft M5 Jam Nut x 2
Trimcraft M5 BSC x 34
Trimcraft M3 SCS x 8
SFJ10-435 x 2
Z_Axis_Shaft_Mount_A x 4
Z_Axis_Shaft_Mount_B x 4
Trimcraft M5 Nylock Nut x 12
Aluminum_Heat_Spreader_Build_Plate
320x320_120VAC_500W_Heated_Bed
HFSB5-2020-321 x 2
92125A226_TYPE 18-8 SS FLAT-HEAD SOCKET CAP SCREW x 4
9002T427 - Mcmaster (Compressed) x 4
5mm_Wingnut(McMaster_94545A225) x 4
Trimcraft M5 Fender Washer x 4
Trimcraft M5 Washer x 8
Bed Mount Block v1-2 x 4
Trimcraft M3 Washer
Trimcraft M3 BSC
BedThermistor

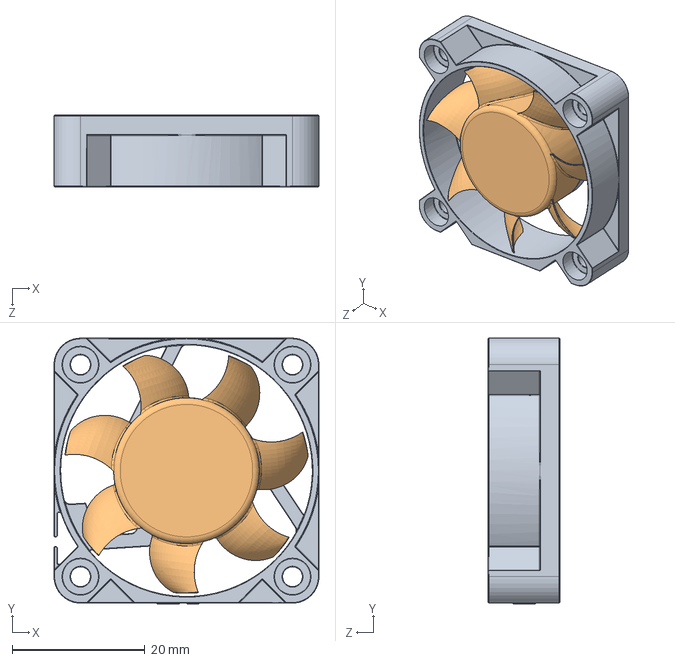
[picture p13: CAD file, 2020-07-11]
3D Models/Solidworks/Electronics/Ultimachines/Jamicon_KF0410-01.SLDASM
40.0 x 40.1 x 10.8 mm
Jamicon_KF0410-01_Case
Jamicon_KF0410-01_Rotor

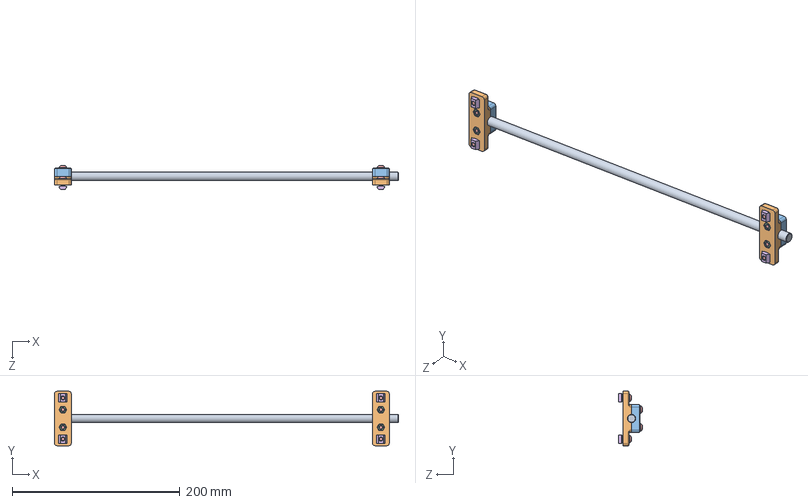
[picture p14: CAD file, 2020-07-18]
3D Models/Solidworks/Sub Assemblies/Z_Rod_And_Mounts.SLDASM
410.0 x 65.0 x 28.5 mm
SFJ10-435
Z_Axis_Shaft_Mount_A x 2
Z_Axis_Shaft_Mount_B x 2
Trimcraft M5 Nylock Nut x 4
Trimcraft M5 BSC x 8
M5 Tslot Nut x 4

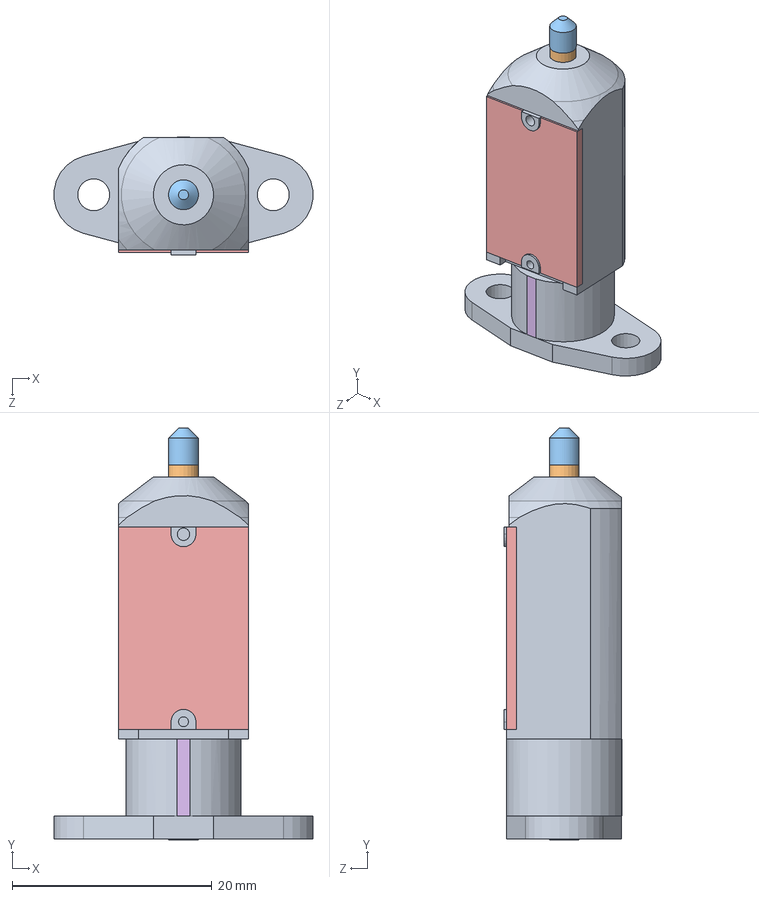
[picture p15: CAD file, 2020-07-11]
3D Models/Solidworks/Electronics/BLTouch.sldasm
25.9 x 41.3 x 11.8 mm
Pin
M4 grub
BLTouch Classic
BLTouch Classic-0
BLTouch Classic-1

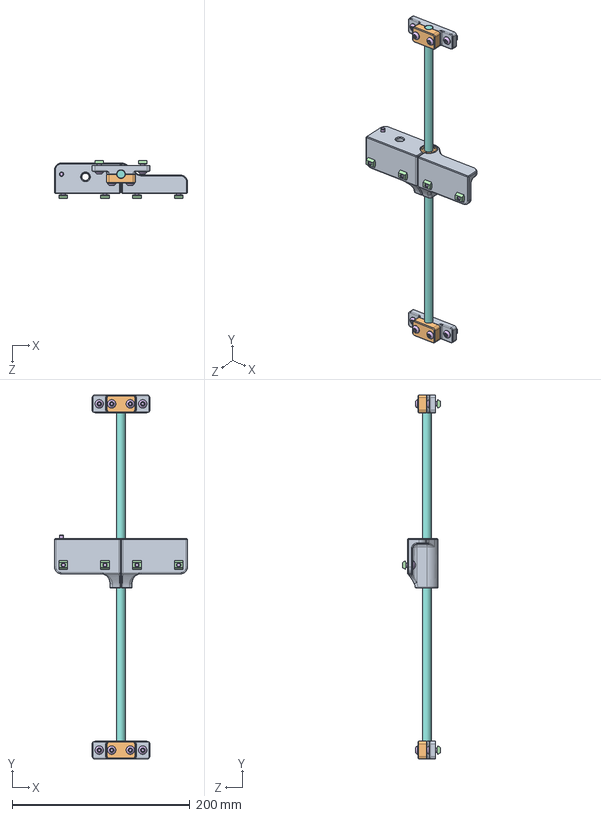
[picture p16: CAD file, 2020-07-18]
3D Models/Solidworks/Sub Assemblies/Z_Axis_Bed_Support.SLDASM
150.0 x 410.0 x 43.0 mm
Z_Axis_Bed_Support V2.5
LM10LUU
TR8x8 POM Lead Nut
M5 Tslot Nut x 8
Trimcraft M5 Jam Nut
Trimcraft M5 BSC x 13
Trimcraft M3 SCS x 4
SFJ10-435
Z_Axis_Shaft_Mount_A x 2
Z_Axis_Shaft_Mount_B x 2
Trimcraft M5 Nylock Nut x 4

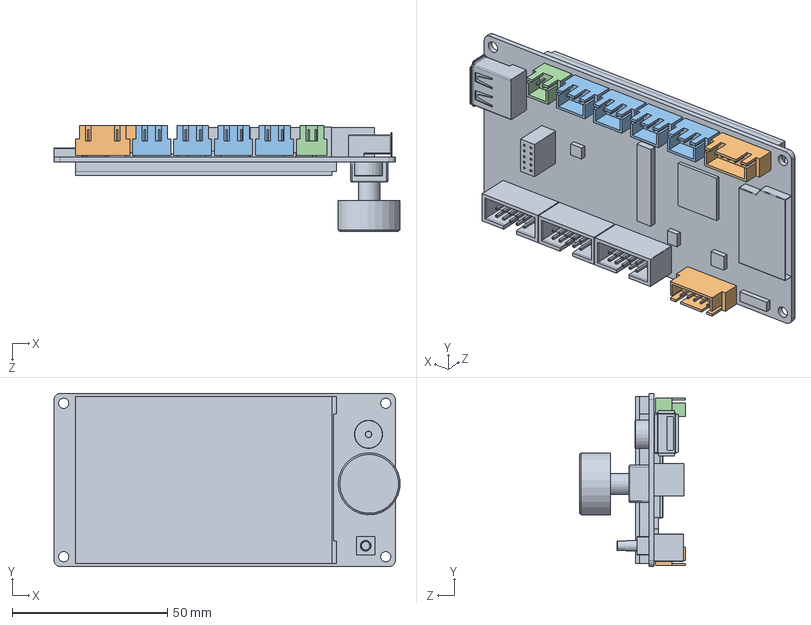
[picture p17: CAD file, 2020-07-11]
3D Models/Solidworks/Electronics/BTT/BTT TFT35 V3 Cover/BIGTREETECH TFT35 V3.SLDASM
111.5 x 55.8 x 34.2 mm
TFT 3.5 V3 +WIFI
KONEKTOR TFT35 PIN5 x 2
KONEKTOR TFT35 PIN3 x 4
KONEKTOR TFT35 PIN2

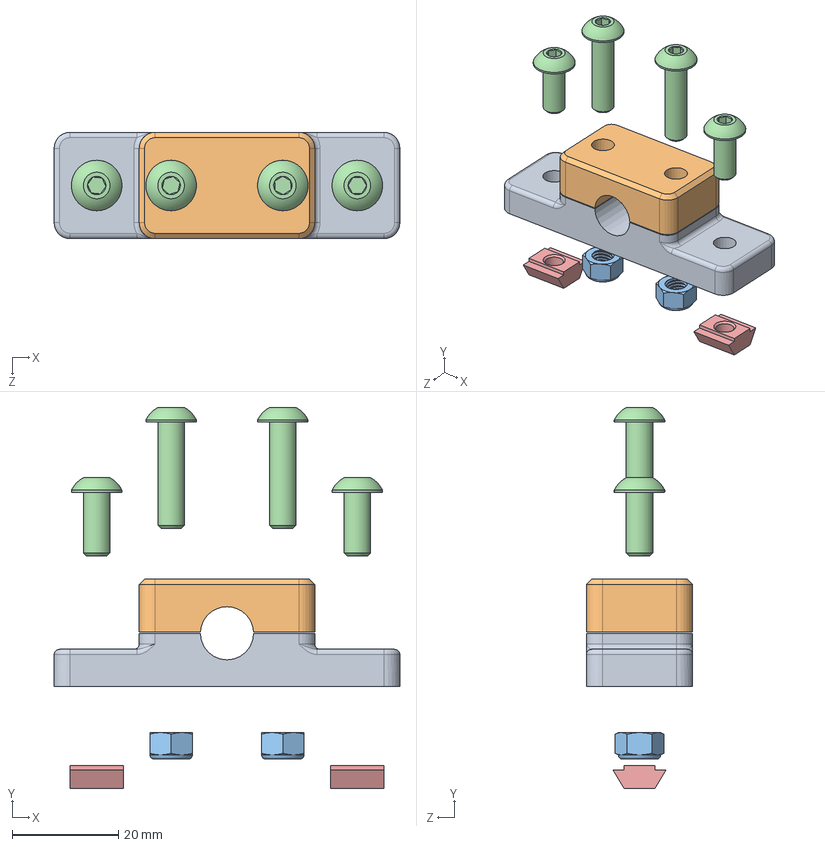
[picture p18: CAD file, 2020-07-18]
3D Models/Solidworks/Sub Assemblies/Z Rod Shaft Mount.sldasm
65.0 x 71.6 x 20.0 mm
Z_Axis_Shaft_Mount_A
Z_Axis_Shaft_Mount_B
Trimcraft M5 Nylock Nut x 2
Trimcraft M5 BSC x 4
M5 Tslot Nut x 2

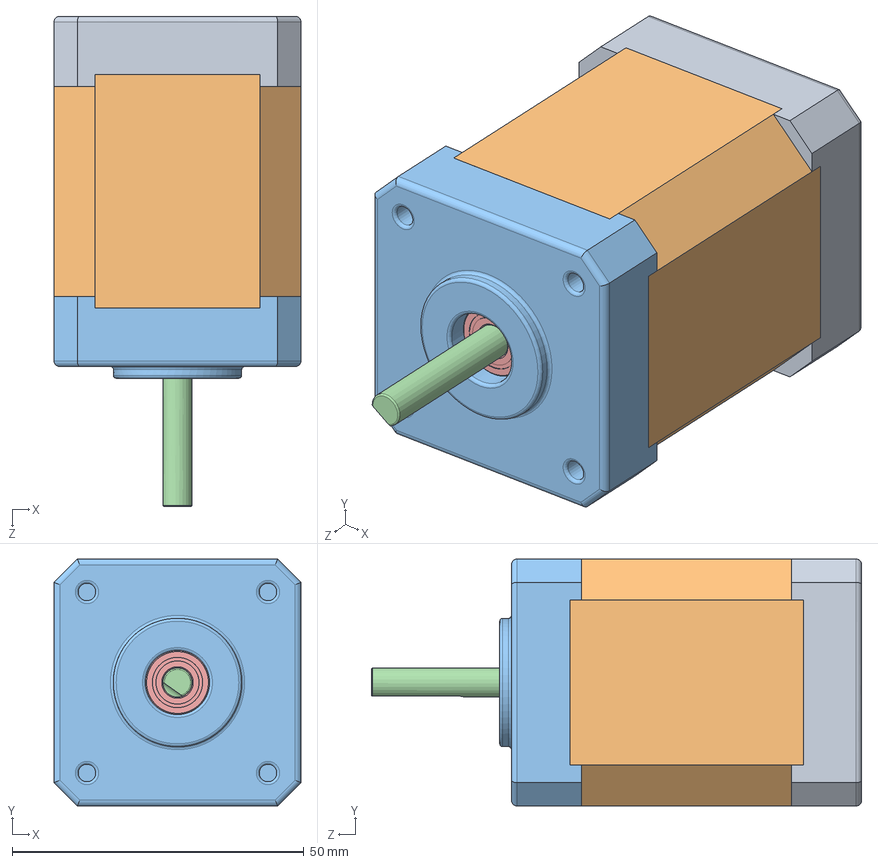
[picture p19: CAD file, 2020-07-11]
3D Models/Solidworks/Robotdigg/NEMA_17_60mm_1.5A.SLDASM
42.3 x 42.3 x 84.0 mm
Base
Body_60mm
FaceCap
Shaft_60mm
7804K107_STAINLESS STEEL BALL BEARING x 2
3mmX50mm_Sockethead(McMaster_91290A137) x 4

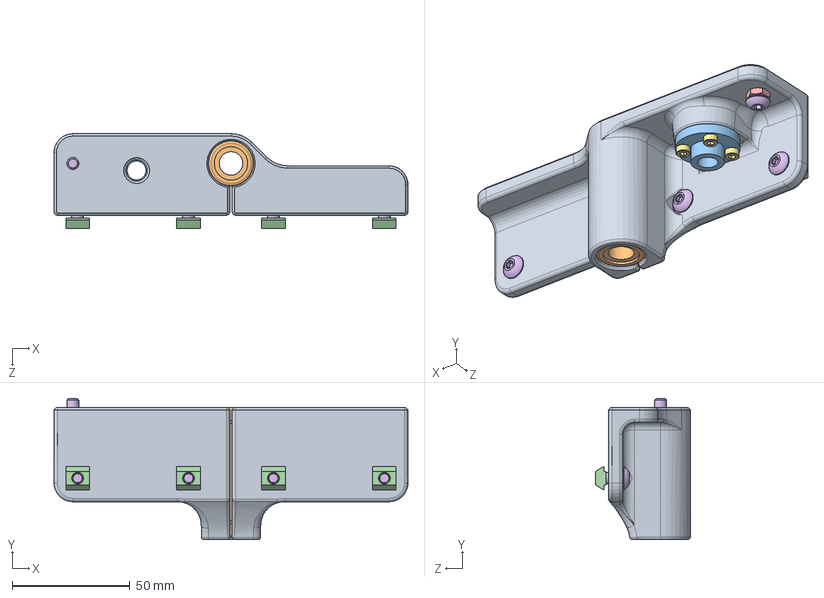
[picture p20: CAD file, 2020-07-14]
3D Models/Solidworks/Sub Assemblies/Bed Support ASMB.sldasm
150.0 x 59.8 x 40.1 mm
Z_Axis_Bed_Support V2.5
LM10LUU
TR8x8 POM Lead Nut
M5 Tslot Nut x 4
Trimcraft M5 Jam Nut
Trimcraft M5 BSC x 5
Trimcraft M3 SCS x 4

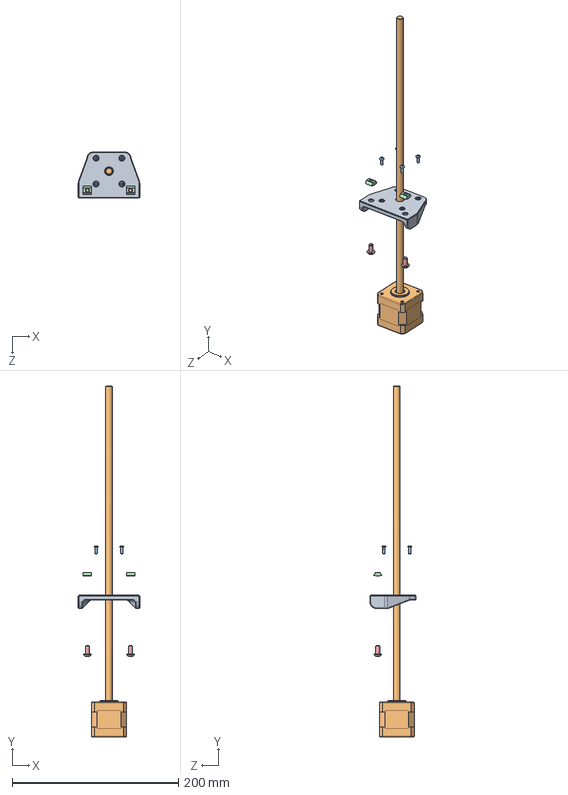
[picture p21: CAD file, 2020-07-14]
3D Models/Solidworks/Sub Assemblies/Z_Motor_ASMB.SLDASM
74.0 x 422.0 x 55.6 mm
Z_Integrated_Leadscrew_Motor_Mount
380mm_TR8x8_42mm_Nema17
Trimcraft M3 BSC x 4
M5 Tslot Nut x 2
Trimcraft M5 BSC x 2

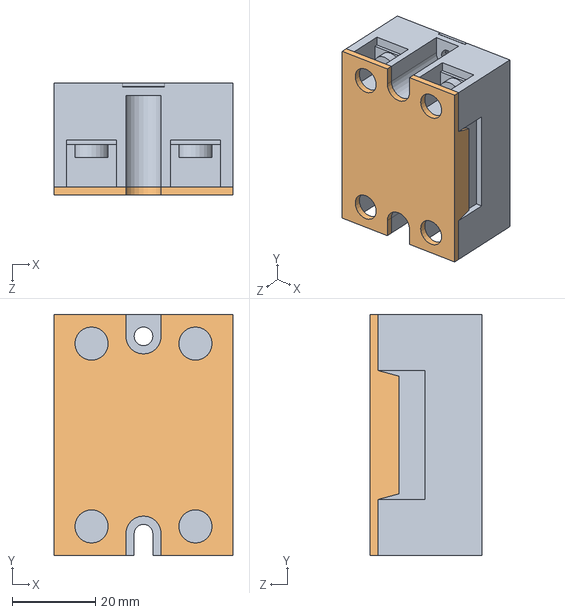
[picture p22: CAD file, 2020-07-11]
3D Models/Solidworks/Electronics/G3NA_220B.SLDASM
43.0 x 58.0 x 27.0 mm
G3NA_220B_BASE
G3NA_220B_COVER

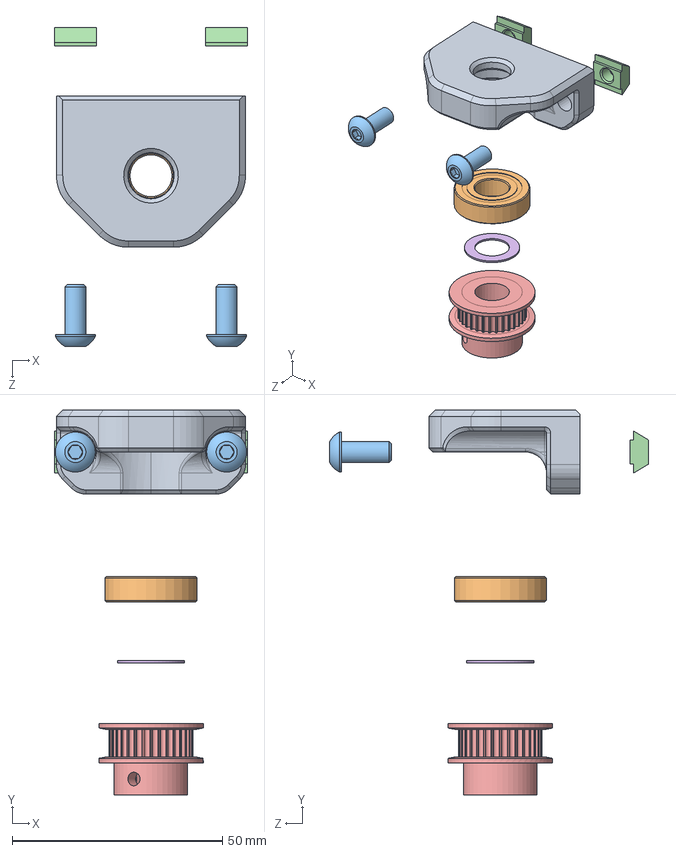
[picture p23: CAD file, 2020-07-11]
3D Models/Solidworks/Sub Assemblies/10mm_Rod_End_Bearing_Assembly.SLDASM
46.0 x 91.6 x 75.8 mm
Bearing_Holder v1-0
6900-2RS_10x22x6
Trimcraft M5 BSC x 2
M5 Tslot Nut x 2
GT2_Aluminum_Timing_Pulley_32_Tooth
10mmx16mmx0.5mm_SHim(McMaster_90214A422)

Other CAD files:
3D Models/Solidworks/Electronics/E3D/V6 Model/V6-Heatblock.sldasm
3D Models/Solidworks/Sub Assemblies/X_Axis_Endstop (New).SLDASM
3D Models/Solidworks/Sub Assemblies/Z Endstop.SLDASM
3D Models/Solidworks/Sub Assemblies/Motor_Mount_With_Nema17_60mm.SLDASM
3D Models/STL/Additional Threaded Spool Holders/18mm_Non-Bearing_Spool_Hub_fixed.STL
3D Models/STL/Additional Threaded Spool Holders/30OD_125L_Non-Bearing_Spool_Hub.STL
3D Models/STL/Additional Threaded Spool Holders/30OD_95L_Non-Bearing_Spool_Hub.STL
3D Models/STL/Additional Threaded Spool Holders/32mm_Non-Bearing_Spool_HubV2.STL
3D Models/STL/Additional Threaded Spool Holders/37mm_Non-Bearing_Spool_Hub_fixed.STL
3D Models/STL/Additional Threaded Spool Holders/50mm_Non-Bearing_Spool_Hub_fixed.STL
3D Models/STL/Additional Threaded Spool Holders/60OD_88L_Non-Bearing_Spool_Hub.STL
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

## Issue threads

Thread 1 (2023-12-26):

What are the Slicer Settings for this printer?

NWalen, 2023-12-26:
I have the Start and End Gcode set but now i just need the speed Settings such as acceleration and what speed to print at.

eclsnowman, 2023-12-27:
Are you still running the old Marlin configuration 2.0.7, newer Marlin like 2.1.2.1 with I.S. enabled, or have you switched to Klipper? Input Shaping can vary the commanded print speeds and accelerations I use pretty dramatically. Secondly, what slicer and print material are you currently trying to tune in? Print settings can vary fairly extensively depending on print shape, layer size (hence max flow rates), and each slicer has some unique features which may change the speeds I utilize.

NWalen, 2023-12-27:
I am running Marlin 2.0.7 but im working on Marlin 2.1.2.1 For filament runout. I use OrcaSlicer With PLA+

NWalen, 2023-12-27:
And im using the Default Marlin Setup in OrcaSlicer

Closed 2023-12-27.

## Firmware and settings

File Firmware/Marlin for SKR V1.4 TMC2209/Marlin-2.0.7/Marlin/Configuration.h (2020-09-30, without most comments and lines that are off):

#pragma once
#define CONFIGURATION_H_VERSION 020007
#define STRING_CONFIG_H_AUTHOR "(LIEN3D, Eustathios V1.65)" // Who made the changes.
#define SHOW_BOOTSCREEN
#define SHOW_CUSTOM_BOOTSCREEN
#define SERIAL_PORT -1
#define SERIAL_PORT_2 0
#define BAUDRATE 250000
  #define MOTHERBOARD BOARD_BTT_SKR_V1_4
#define CUSTOM_MACHINE_NAME "Eustathios V2.5"
#define EXTRUDERS 1
#define DEFAULT_NOMINAL_FILAMENT_DIA 1.75
#define TEMP_SENSOR_0 5
#define TEMP_SENSOR_1 0
#define TEMP_SENSOR_2 0
#define TEMP_SENSOR_3 0
#define TEMP_SENSOR_4 0
#define TEMP_SENSOR_5 0
#define TEMP_SENSOR_6 0
#define TEMP_SENSOR_7 0
#define TEMP_SENSOR_BED 11
#define TEMP_SENSOR_PROBE 0
#define TEMP_SENSOR_CHAMBER 0
#define DUMMY_THERMISTOR_998_VALUE 25
#define DUMMY_THERMISTOR_999_VALUE 100
#define MAX_REDUNDANT_TEMP_SENSOR_DIFF 10
#define TEMP_RESIDENCY_TIME     10  // (seconds) Time to wait for hotend to "settle" in M109
#define TEMP_WINDOW              5  // (°C) Temperature proximity for the "temperature reached" timer
#define TEMP_HYSTERESIS          8  // (°C) Temperature proximity considered "close enough" to the target
#define TEMP_BED_RESIDENCY_TIME 10  // (seconds) Time to wait for bed to "settle" in M190
#define TEMP_BED_WINDOW          5  // (°C) Temperature proximity for the "temperature reached" timer
#define TEMP_BED_HYSTERESIS      8  // (°C) Temperature proximity considered "close enough" to the target
#define HEATER_0_MINTEMP   3
#define HEATER_1_MINTEMP   3
#define HEATER_2_MINTEMP   3
#define HEATER_3_MINTEMP   3
#define HEATER_4_MINTEMP   3
#define HEATER_5_MINTEMP   3
#define HEATER_6_MINTEMP   3
#define HEATER_7_MINTEMP   3
#define BED_MINTEMP        3
#define HEATER_0_MAXTEMP 300
#define HEATER_1_MAXTEMP 300
#define HEATER_2_MAXTEMP 300
#define HEATER_3_MAXTEMP 300
#define HEATER_4_MAXTEMP 300
#define HEATER_5_MAXTEMP 300
#define HEATER_6_MAXTEMP 300
#define HEATER_7_MAXTEMP 300
#define BED_MAXTEMP      150
#define PIDTEMP
#define BANG_MAX 255     // Limits current to nozzle while in bang-bang mode; 255=full current
#define PID_MAX BANG_MAX // Limits current to nozzle while PID is active (see PID_FUNCTIONAL_RANGE below); 255=full current
#define PID_K1 0.95      // Smoothing factor within any PID loop
  #define PID_AUTOTUNE_MENU     // Add PID auto-tuning to the "Advanced Settings" menu. (~250 bytes of PROGMEM)
    #define DEFAULT_Kp  22.60
    #define DEFAULT_Ki   1.83
    #define DEFAULT_Kd   69.66
#define PIDTEMPBED
#define MAX_BED_POWER 255 // limits duty cycle to bed; 255=full current
  #define DEFAULT_bedKp 290.10
  #define DEFAULT_bedKi 47.60
  #define DEFAULT_bedKd 442.03
  #define PID_FUNCTIONAL_RANGE 10 // If the temperature difference between the target temperature and the actual temperature
#define PREVENT_COLD_EXTRUSION
#define EXTRUDE_MINTEMP 170
#define PREVENT_LENGTHY_EXTRUDE
#define EXTRUDE_MAXLENGTH 1100
#define THERMAL_PROTECTION_HOTENDS // Enable thermal protection for all extruders
#define THERMAL_PROTECTION_BED     // Enable thermal protection for the heated bed
#define USE_XMIN_PLUG
#define USE_YMIN_PLUG
#define USE_ZMIN_PLUG
#define ENDSTOPPULLUPS
#define X_MIN_ENDSTOP_INVERTING true // Set to true to invert the logic of the endstop.
#define Y_MIN_ENDSTOP_INVERTING true // Set to true to invert the logic of the endstop.
#define Z_MIN_ENDSTOP_INVERTING true // Set to true to invert the logic of the endstop.
#define X_MAX_ENDSTOP_INVERTING false // Set to true to invert the logic of the endstop.
#define Y_MAX_ENDSTOP_INVERTING false // Set to true to invert the logic of the endstop.
#define Z_MAX_ENDSTOP_INVERTING false // Set to true to invert the logic of the endstop.
#define Z_MIN_PROBE_ENDSTOP_INVERTING false // Set to true to invert the logic of the probe.
#define X_DRIVER_TYPE  TMC2209
#define Y_DRIVER_TYPE  TMC2209
#define Z_DRIVER_TYPE  TMC2209
#define Z2_DRIVER_TYPE TMC2209
#define E0_DRIVER_TYPE TMC2209
#define DEFAULT_AXIS_STEPS_PER_UNIT   { 160, 160, 800, 830 }  // 1.8deg x 20tooth x 32microstep XandY, 1.8deg x 8mm pitch x32 microstep Z, BMG on 32microstep = 830
#define DEFAULT_MAX_FEEDRATE          { 180, 180, 16, 120 }
#define DEFAULT_MAX_ACCELERATION      { 2000, 2000, 500, 3000 }
#define DEFAULT_ACCELERATION          2000    // X, Y, Z and E acceleration for printing moves
#define DEFAULT_RETRACT_ACCELERATION  5000    // E acceleration for retracts
#define DEFAULT_TRAVEL_ACCELERATION   2000    // X, Y, Z acceleration for travel (non printing) moves
#define DEFAULT_EJERK    5.0  // May be used by Linear Advance
  #define JUNCTION_DEVIATION_MM 0.04 // (mm) Distance from real junction edge
  #define JD_HANDLE_SMALL_SEGMENTS    // Use curvature estimation instead of just the junction angle
#define S_CURVE_ACCELERATION
#define Z_MIN_PROBE_USES_Z_MIN_ENDSTOP_PIN
#define USE_PROBE_FOR_Z_HOMING
#define BLTOUCH
#define NOZZLE_TO_PROBE_OFFSET { 28, 3, -1.78 }
#define PROBING_MARGIN 5
#define XY_PROBE_SPEED (100*60)
#define Z_PROBE_SPEED_FAST (HOMING_FEEDRATE_Z * 2)
#define Z_PROBE_SPEED_SLOW (HOMING_FEEDRATE_Z)
#define Z_CLEARANCE_DEPLOY_PROBE    8 // Z Clearance for Deploy/Stow
#define Z_CLEARANCE_BETWEEN_PROBES  5 // Z Clearance between probe points
#define Z_CLEARANCE_MULTI_PROBE     5 // Z Clearance between multiple probes
#define Z_PROBE_LOW_POINT          -3 // Farthest distance below the trigger-point to go before stopping
#define Z_PROBE_OFFSET_RANGE_MIN -20
#define Z_PROBE_OFFSET_RANGE_MAX 20
#define Z_MIN_PROBE_REPEATABILITY_TEST
#define X_ENABLE_ON 0
#define Y_ENABLE_ON 0
#define Z_ENABLE_ON 0
#define E_ENABLE_ON 0 // For all extruders
#define DISABLE_X false
#define DISABLE_Y false
#define DISABLE_Z false
#define DISABLE_E false             // Disable the extruder when not stepping
#define DISABLE_INACTIVE_EXTRUDER   // Keep only the active extruder enabled
#define INVERT_X_DIR true
#define INVERT_Y_DIR false
#define INVERT_Z_DIR true
#define INVERT_E0_DIR true
#define INVERT_E1_DIR false
#define INVERT_E2_DIR false
#define INVERT_E3_DIR false
#define INVERT_E4_DIR false
#define INVERT_E5_DIR false
#define INVERT_E6_DIR false
#define INVERT_E7_DIR false
#define X_HOME_DIR -1
#define Y_HOME_DIR -1
#define Z_HOME_DIR -1
#define X_BED_SIZE 300
#define Y_BED_SIZE 300
#define X_MIN_POS 0
#define Y_MIN_POS 0
#define Z_MIN_POS 0
#define X_MAX_POS X_BED_SIZE
#define Y_MAX_POS Y_BED_SIZE
#define Z_MAX_POS 300
#define MIN_SOFTWARE_ENDSTOPS
  #define MIN_SOFTWARE_ENDSTOP_X
  #define MIN_SOFTWARE_ENDSTOP_Y
  #define MIN_SOFTWARE_ENDSTOP_Z
#define MAX_SOFTWARE_ENDSTOPS
  #define MAX_SOFTWARE_ENDSTOP_X
  #define MAX_SOFTWARE_ENDSTOP_Y
  #define MAX_SOFTWARE_ENDSTOP_Z
#define AUTO_BED_LEVELING_BILINEAR
#define RESTORE_LEVELING_AFTER_G28
  #define ENABLE_LEVELING_FADE_HEIGHT
  #define SEGMENT_LEVELED_MOVES
  #define LEVELED_SEGMENT_LENGTH 5.0 // (mm) Length of all segments (except the last one)
  #define GRID_MAX_POINTS_X 5
  #define GRID_MAX_POINTS_Y GRID_MAX_POINTS_X
    #define EXTRAPOLATE_BEYOND_GRID
#define LCD_BED_LEVELING
  #define MESH_EDIT_Z_STEP  0.025 // (mm) Step size while manually probing Z axis.
  #define LCD_PROBE_Z_RANGE 4     // (mm) Z Range centered on Z_MIN_POS for LCD Z adjustment
#define LEVEL_BED_CORNERS
  #define LEVEL_CORNERS_INSET_LFRB { 30, 30, 30, 30 } // (mm) Left, Front, Right, Back insets
  #define LEVEL_CORNERS_HEIGHT      0.0   // (mm) Z height of nozzle at leveling points
  #define LEVEL_CORNERS_Z_HOP       4.0   // (mm) Z height of nozzle between leveling points
  #define LEVEL_CENTER_TOO              // Move to the center after the last corner
#define Z_PROBE_END_SCRIPT "G1 X4 Y4 F8000"
#define Z_SAFE_HOMING
  #define Z_SAFE_HOMING_X_POINT X_CENTER  // X point for Z homing
  #define Z_SAFE_HOMING_Y_POINT Y_CENTER  // Y point for Z homing
#define HOMING_FEEDRATE_XY (50*60)
#define HOMING_FEEDRATE_Z  (8*60)
#define VALIDATE_HOMING_ENDSTOPS
#define EEPROM_SETTINGS     // Persistent storage with M500 and M501
#define EEPROM_CHITCHAT       // Give feedback on EEPROM commands. Disable to save PROGMEM.
#define EEPROM_BOOT_SILENT    // Keep M503 quiet and only give errors during first load
  #define EEPROM_AUTO_INIT  // Init EEPROM automatically on any errors.
#define HOST_KEEPALIVE_FEATURE        // Disable this if your host doesn't like keepalive messages
#define DEFAULT_KEEPALIVE_INTERVAL 2  // Number of seconds between "busy" messages. Set with M113.
#define BUSY_WHILE_HEATING            // Some hosts require "busy" messages even during heating
#define PREHEAT_1_LABEL       "PLA"
#define PREHEAT_1_TEMP_HOTEND 200
#define PREHEAT_1_TEMP_BED     60
#define PREHEAT_1_FAN_SPEED     0 // Value from 0 to 255
#define PREHEAT_2_LABEL       "PETG"
#define PREHEAT_2_TEMP_HOTEND 230
#define PREHEAT_2_TEMP_BED     70
#define PREHEAT_2_FAN_SPEED     0 // Value from 0 to 255
#define NOZZLE_PARK_FEATURE
  #define NOZZLE_PARK_POINT { (X_MIN_POS + 10), (Y_MAX_POS - 10), 10 }
  #define NOZZLE_PARK_Z_RAISE_MIN   2   // (mm) Always raise Z by at least this distance
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

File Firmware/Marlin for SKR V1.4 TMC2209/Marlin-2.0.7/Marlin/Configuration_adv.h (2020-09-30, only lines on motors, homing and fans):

#define E0_AUTO_FAN_PIN -1
#define E1_AUTO_FAN_PIN -1
#define E2_AUTO_FAN_PIN -1
#define E3_AUTO_FAN_PIN -1
#define E4_AUTO_FAN_PIN -1
#define E5_AUTO_FAN_PIN -1
#define E6_AUTO_FAN_PIN -1
#define E7_AUTO_FAN_PIN -1
#define CHAMBER_AUTO_FAN_PIN -1
#define HOMING_BUMP_MM      { 5, 5, 2 }       // (mm) Backoff from endstops after first bump
#define HOMING_BUMP_DIVISOR { 2, 2, 4 }       // Re-Bump Speed Divisor (Divides the Homing Feedrate)
  #define HOME_AFTER_G34
#define MICROSTEP_MODES { 16, 16, 16, 16, 16, 16 } // [1,2,4,8,16]
#define ADVANCED_PAUSE_FEATURE
  #define ADVANCED_PAUSE_PURGE_FEEDRATE        3  // (mm/s) Extrude feedrate (after loading). Should be slower than load feedrate.
  #define ADVANCED_PAUSE_PURGE_LENGTH         50  // (mm) Length to extrude after loading.
  #define ADVANCED_PAUSE_RESUME_PRIME          0  // (mm) Extra distance to prime nozzle after returning from park.
    #define X_CURRENT       950        // (mA) RMS current. Multiply by 1.414 for peak current.
    #define X_CURRENT_HOME  X_CURRENT  // (mA) RMS current for sensorless homing
    #define X_MICROSTEPS     32    // 0..256
    #define Y_CURRENT       950
    #define Y_CURRENT_HOME  Y_CURRENT
    #define Y_MICROSTEPS     32
    #define Z_CURRENT       800
    #define Z_CURRENT_HOME  Z_CURRENT
    #define Z_MICROSTEPS     32
    #define Z2_CURRENT      800
    #define Z2_CURRENT_HOME Z2_CURRENT
    #define Z2_MICROSTEPS    32
    #define E0_CURRENT      800
    #define E0_MICROSTEPS    32
    #define CURRENT_STEP_DOWN     50  // [mA]
    #define REPORT_CURRENT_CHANGE
  #define X_HYBRID_THRESHOLD     100  // [mm/s]
  #define X2_HYBRID_THRESHOLD    100
  #define Y_HYBRID_THRESHOLD     100
  #define Y2_HYBRID_THRESHOLD    100
  #define Z_HYBRID_THRESHOLD       3
  #define Z2_HYBRID_THRESHOLD      3
  #define Z3_HYBRID_THRESHOLD      3
  #define Z4_HYBRID_THRESHOLD      3
  #define E0_HYBRID_THRESHOLD     30
  #define E1_HYBRID_THRESHOLD     30
  #define E2_HYBRID_THRESHOLD     30
  #define E3_HYBRID_THRESHOLD     30
  #define E4_HYBRID_THRESHOLD     30
  #define E5_HYBRID_THRESHOLD     30
  #define E6_HYBRID_THRESHOLD     30
  #define E7_HYBRID_THRESHOLD     30

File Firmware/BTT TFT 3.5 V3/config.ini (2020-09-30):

#### Default Config file for BigTreeTech TFT Controllers
#
# BIGTREE_TFT35_V1_1 / BIGTREE_TFT35_V1_2    / BIGTREE_TFT35_V2_0
# BIGTREE_TFT35_V3_0 / BIGTREE_TFT35_E3_V3_0 / BIGTREE_TFT28_V1_0
# BIGTREE_TFT28_V3_0 / BIGTREE_TFT24_V1_1    / MKS_32_V1_4
#
# Firmware Source: https://github.com/bigtreetech/BIGTREETECH-TouchScreenFirmware


#--------------------------------------------------------------------
# Supported Marlin Firmware Version
#--------------------------------------------------------------------
#  Minimum Marlin Firmware Version: Bugfix-2.0.x
#  Distribution date: 2020-05-12
#  Source: https://github.com/MarlinFirmware/Marlin/tree/bugfix-2.0.x


#--------------------------------------------------------------------
# General Settings
#--------------------------------------------------------------------

#### UNIFIED MENU / CLASSIC MENU
# Select a UI Menu flavour
# Options: [Unified Menu: 1, Classic Menu: 0]
unified_menu:1

#### Baudrate
# Options: [2400: 0, 9600: 1, 19200: 2, 38400: 3, 57600: 4, 115200: 5, 250000: 6, 500000: 7, 1000000: 8]
baudrate:6

#### Default Touch Mode Language
# Select the language to display on the LCD while in Touch Mode.
# Options: [ENGLISH: 0,  CHINESE: 1,     RUSSIAN: 2,  JAPANESE: 3,    ARMENIAN: 4,
#            GERMAN: 5,    CZECH: 6,       SPAIN: 7,    FRENCH: 8,  PORTUGUESE: 9,
#           ITALIAN: 10,  POLISH: 11,     SLOVAK: 12,    DUTCH: 13,  HUNGARIAN: 14,
#           TURKISH: 15,   GREEK: 16,  SLOVENIAN: 17,  CATALAN: 18]
language:0

#### Default Touch Mode Color Options
# Options: [ WHITE: 0,  BLACK: 1,  RED: 2,  GREEN: 3,      BLUE: 4,       CYAN: 5,  MAGENTA: 6,    YELLOW: 7,
#           ORANGE: 8, PURPLE: 9, LIME: 10, BROWN: 11, DARKBLUE: 12, DARKGREEN: 13,    GRAY: 14, DARKGRAY: 15]
# Or set the color(RGB888 format) hex value directly(start with “0x”).
# Such as: 0xFF0000 : Red, 0x00FF00 : Green, 0x0000FF : Blue
# Title background color
title_back_color:1

# Background color
background_color:1

# Font foreground color
font_color:0

# Reminder font color, such as: "No print attached", "Busy processing", etc.
reminder_color:2

# Volume status/reminder font color, such as: "Card inserted", "Card removed"
volume_status_color:5

# Backgroud color for X Y Z position display in Status Screen.
status_xyz_bg_color:15

# List View Border Color
list_border_color:15

# List View button background color
list_button_bg_color:15

#### Rotate UI 180 degrees
# Options: [enable: 1, disable: 0]
rotate_ui:0

#### Show or hide Temperature ACK in Gcode Terminal
# Options: [Show: 1, Hide: 0]
terminal_ack:0

#### invert X axis button function in Move menu to match move buttons to actual axis
# Options: [enable: 1, disable: 0]
# Invert Axis format      [ X<option> Y<option> Z<option> E<option>]
invert_axis:X0 Y0 Z0

#### Persistent temperature info
# show persistent temperature info on all menu screens
# Options: [enable: 1, disable: 0]
persistent_info:0

#### File List Mode
# show file as list
# Options: [enable: 1, disable: 0]
files_list_mode:1

#### Notification style for ACK messages
# Set the notification style to use for displaying the ACK messages which start with 'echo:'
#
# NOTE: The OFF value is applied to any ACK message type (e.g. even to known echo ACK).
#       It means that any kind of ACK message is silently discard
#
# Options: [OFF: 0, POPUP: 1, TOAST: 2]
#   OFF:   No notification. The message is ignored.
#   POPUP: Display a popup window for user confirmation.
#   TOAST: A non-blocking Toast notification is displayed for few seconds. No user interaction is needed
ack_notification:1

#--------------------------------------------------------------------
# Marlin Mode Settings (Only for TFT24_V1.1 & TFT28/TFT35/TFT43/TFT50/TFT70_V3.0)
#--------------------------------------------------------------------

#### Default Mode
# Options: [0: Marlin Mode, 1: Touch Mode]
default_mode:1

#### Keep Serial Always ON
# Keep UART (Serial communication) alive in Marlin Mode
# Allow seamless OctoPrint UART connection to the TFT's UART/serial expansion port no matter which mode the TFT is in.
# Options: [0: Disabled, 1: Enabled]
serial_always_on:0

#### Default Marlin Mode Background & Font Color Options
# Options: [ WHITE: 0,  BLACK: 1,  RED: 2,  GREEN: 3,      BLUE: 4,       CYAN: 5,  MAGENTA: 6,    YELLOW: 7,
#           ORANGE: 8, PURPLE: 9, LIME: 10, BROWN: 11, DARKBLUE: 12, DARKGREEN: 13,    GRAY: 14, DARKGRAY: 15]
# Or set the color(RGB888 format) hex value directly(start with “0x”).
# Such as: 0xFF0000 : Red, 0x00FF00 : Green, 0x0000FF : Blue
marlin_bg_color:1
marlin_fn_color:0

#### Marlin Mode show title
# Options: [enable: 1, disable: 0]
marlin_show_title:0

# Run Marlin Mode in Fullscreen
# Options: [enable: 1, disable: 0] [Disabled. RECOMMENDED FOR TFT24]
marlin_fullscreen:1

# Select marlin type
# Options: [LCD12864: 1, LCD2004: 0]
marlin_type:1

#### Text displayed at the top of the TFT in Marlin Mode.
marlin_title:LCD12864 Simulator
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

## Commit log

2020-07-11 Initial Upload of Files
    Initial Upload of Files
    [02_ESV25.DXF, 03_ESV25.DXF, 04_ESV25.DXF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]
2020-07-11 Added Pictures of Printed Parts
    Added Pictures of Printed Parts
2020-07-11 Added Printed Parts to Readme
    Added Printed Parts to Readme
2020-07-11 Added STL's and Additional Parts
    Added STL's and Additional Images
    [18mm_Non-Bearing_Spool_Hub_fixed.STL, 30OD_125L_Non-Bearing_Spool_Hub.STL, 30OD_95L_Non-Bearing_Spool_Hub.STL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]
2020-07-11 Update ES25 BOM.xlsx
    Updated The BOM
    [ES25 BOM.xlsx]
2020-07-14 Updated BOMs and Drawings, John Phan noticed some errors
    Updated Prints and BOM with corrections and additions notice by someone building the printer (John Phan).
    [02_ESV25.DXF, 03_ESV25.DXF, 04_ESV25.DXF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]
2020-07-14 Updated Other Model Formats
    Updated Other Model Formats (X_T, Step, Fusion360). Changes to part numbers and bed extrusions.
2020-07-15 Updated STL's
    Updated the STL's with proper orientations, required diaphragms to avoid supports, and create full plate nested example for all parts required (Too Large for most printeds, needs to be split up).
    [BMG Mount.STL, Bearing Holder with Pass Through (6900-2RS).STL, Center Carriage With BLTouch.STL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]
2020-07-16 Update Eustathios_Spider_V2.5.f3d
    I added Ridged Bodies, Grounding of the frame, and Joints for motion study to the Fusion360 Model. This took me longer than expected because this is an imported model and I had to combine, create com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
2020-07-16 Added clean 1:1 DXF prints for heated bed and acrylic panels
    The DXF detailed prints with title blocks are kind of messy for importing to some cutting programs. So I cleaned them up and scaled them 1:1 in the DXF so they are easy to send to a laser cutter (Acr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
    [ESV25_0.25in(6mm)_Acrylic_1to1.dxf, ESV25_0.25in(6mm)_Cast-Aluminum_1to1.dxf]
2020-07-18 Updated Drawings for Bed Modification
    Updated Drawings for Bed Modification.
    -Hole in Heated Pad made smaller (10x10)
    -Heat Spreader updated for hole for thermistor and m3 retaining bolt and washer to hold thermistor
    -Print for heat spreader and heated pad updated.
    -Add ballon to frame drawing to show detail on sideskirt fan.
    [02_ESV25.DXF, 03_ESV25.DXF, 04_ESV25.DXF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]
2020-07-23 Add more details and links in BOM
    Add Formatting, and more links in BOM. Specifically the heated pad from alibaba. Thank You John Phan for getting Alirubber to add the link.
    [ES25 BOM.xlsx]
2020-09-30 Firmware for Mainboard and TFT
    I have included Marlin 2.0.7 configured for the SKR V1.4 (non-turbo) with 5xTMC2209 drivers, a BL Touch, and Independant drivers on the Z Lead Screws for auto Z Tramming. I have also included a custo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
    [Configuration.h, Configuration_adv.h]
2020-09-30 Fix TFT config.ini Baud Rate to match Printer Baudrate in Marlin
    Fix TFT config.ini Baud Rate to match Printer Baudrate in Marlin
    [config.ini]

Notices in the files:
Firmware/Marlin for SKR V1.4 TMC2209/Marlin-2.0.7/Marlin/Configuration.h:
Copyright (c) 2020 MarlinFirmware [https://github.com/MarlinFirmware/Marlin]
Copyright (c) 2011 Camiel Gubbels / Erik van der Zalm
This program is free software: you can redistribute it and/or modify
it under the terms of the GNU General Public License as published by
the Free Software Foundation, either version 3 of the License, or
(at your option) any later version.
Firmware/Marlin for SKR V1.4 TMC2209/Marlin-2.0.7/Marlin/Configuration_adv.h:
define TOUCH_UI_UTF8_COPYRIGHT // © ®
